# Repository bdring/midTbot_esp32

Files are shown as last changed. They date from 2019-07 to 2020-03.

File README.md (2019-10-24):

# MidTBot ESP32

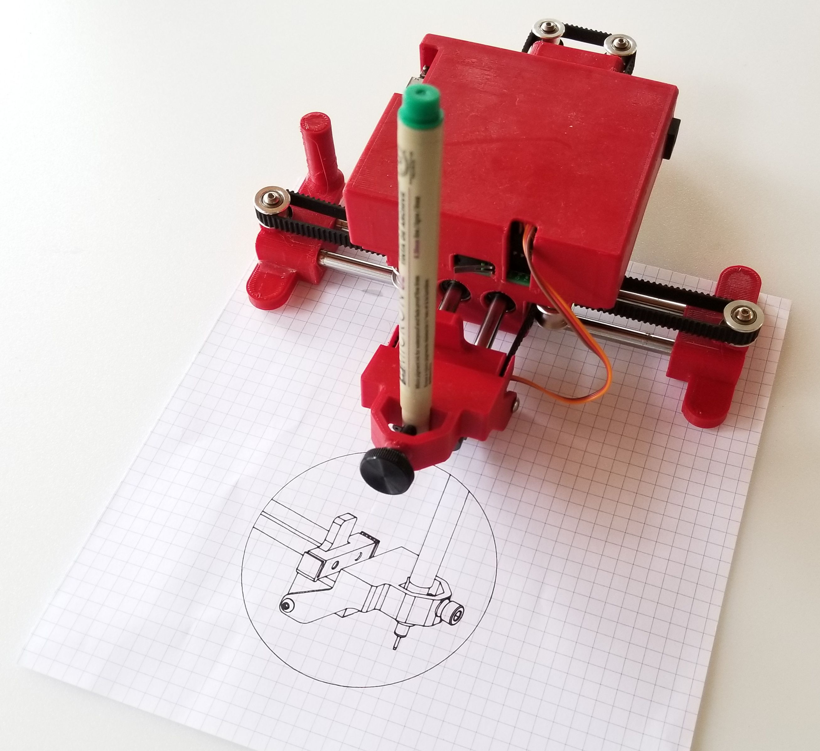
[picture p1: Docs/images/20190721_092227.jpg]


The MidTBot is a small and simple little pen plotter. All of the custom parts are 3D printed. The rest of the parts are low cost and easy to get.

The controller uses an ESP32 running Grbl_ESP32 firmware. It can be controlled via USB, Bluetooth or Wifi. You can simply upload gcode files to the unboard SD card and print.

The machine is controlled by a unique H-bot configuration, that uses a single belt. Two small stepper motors drive that belt in a special way to move in the X/Y plane. The pen is lifted by a hobby servo using a very simple and accurate mechanism.

[Here is a link to a video of the plotter in action.](https://www.youtube.com/watch?v=jiwWCrCfXrY)

The project is open source (Creative commons 4.0 Attribution - Share Alike) and all the files are in this Githob repo. Assembly instructions [are here](https://github.com/bdring/midTbot_esp32/wiki/Assembly-Instructions). If you have questions, please ask them by opening an issue in this repo.

### Check it out on GrabCad

Click on image for interactive viewer in browser.

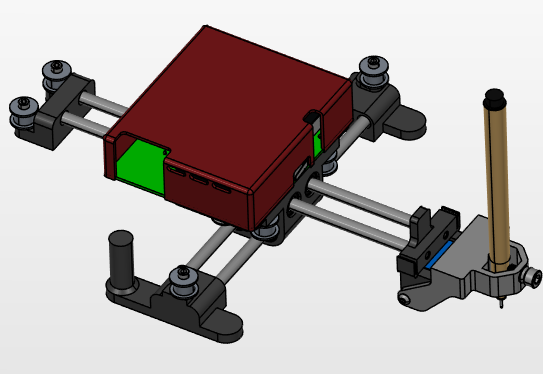
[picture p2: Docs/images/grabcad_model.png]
GrabCAD (https://workbench.grabcad.com/workbench/projects/gcj3zJAQexD3ve_8KkwymatyKXhCWnRs8TB5U1ojGxl3s4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)


### Kits

There currently are no full kits for sale. [Controller kits are available on Tindie](https://www.tindie.com/products/33366583/midtbot-esp32-v1-controller-kit/).

### Donation

This project represents a lot of work. Please consider a safe, secure and highly appreciated donation via the PayPal link below.



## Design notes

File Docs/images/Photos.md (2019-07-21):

### Photos

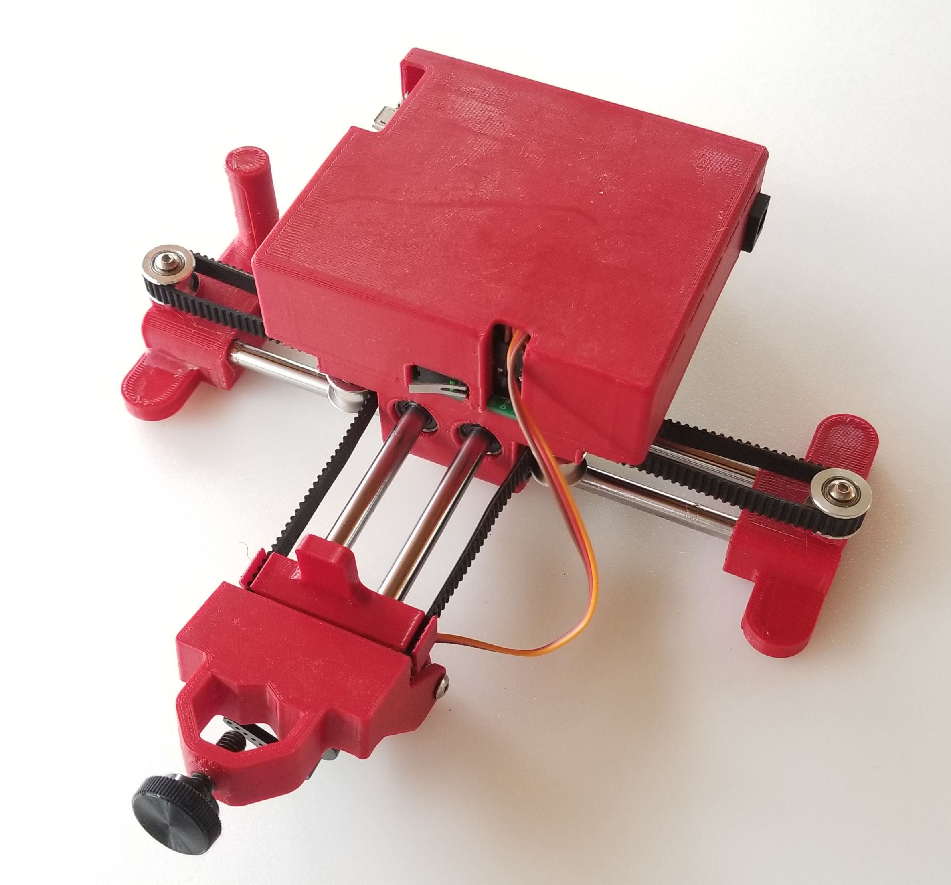
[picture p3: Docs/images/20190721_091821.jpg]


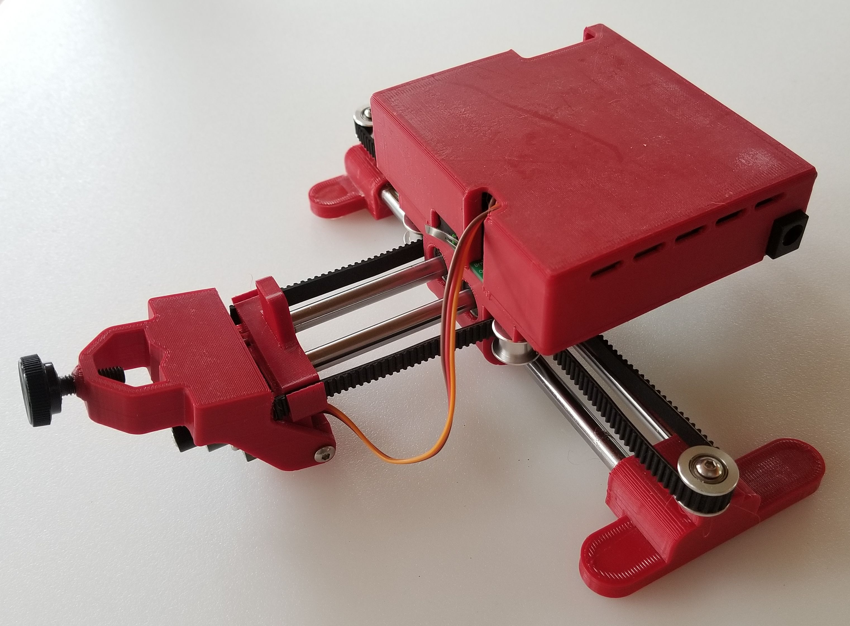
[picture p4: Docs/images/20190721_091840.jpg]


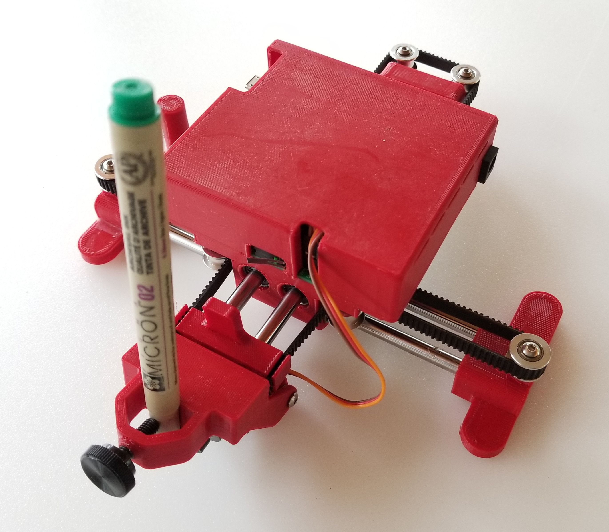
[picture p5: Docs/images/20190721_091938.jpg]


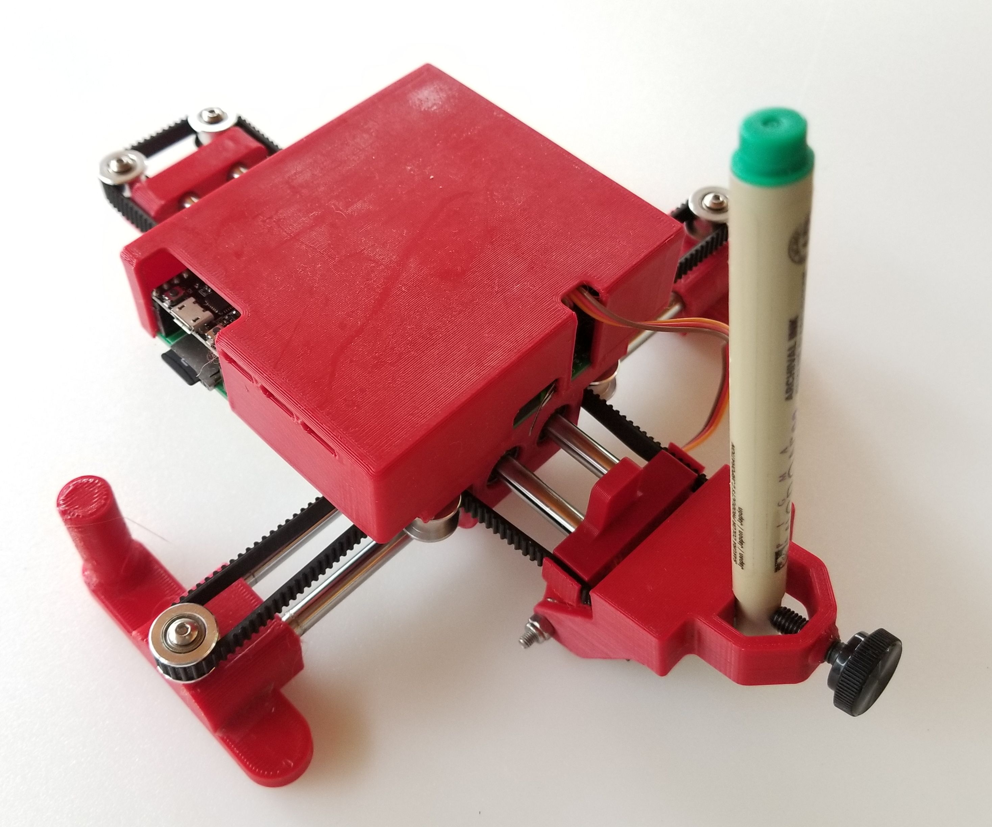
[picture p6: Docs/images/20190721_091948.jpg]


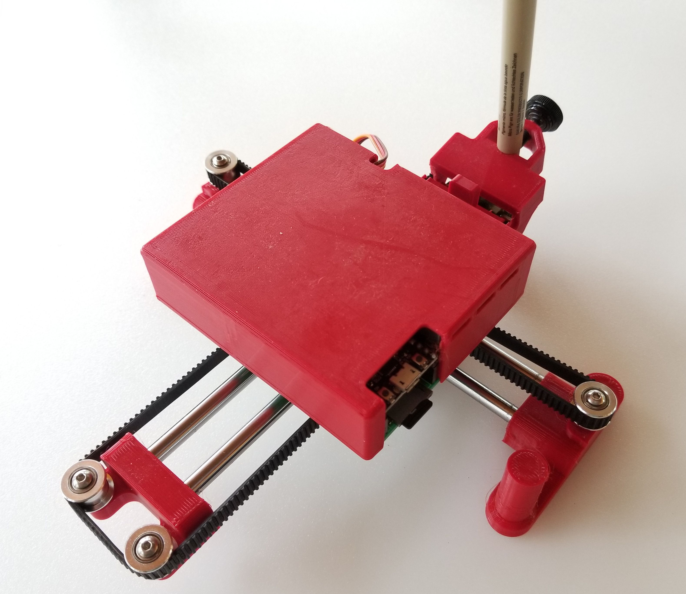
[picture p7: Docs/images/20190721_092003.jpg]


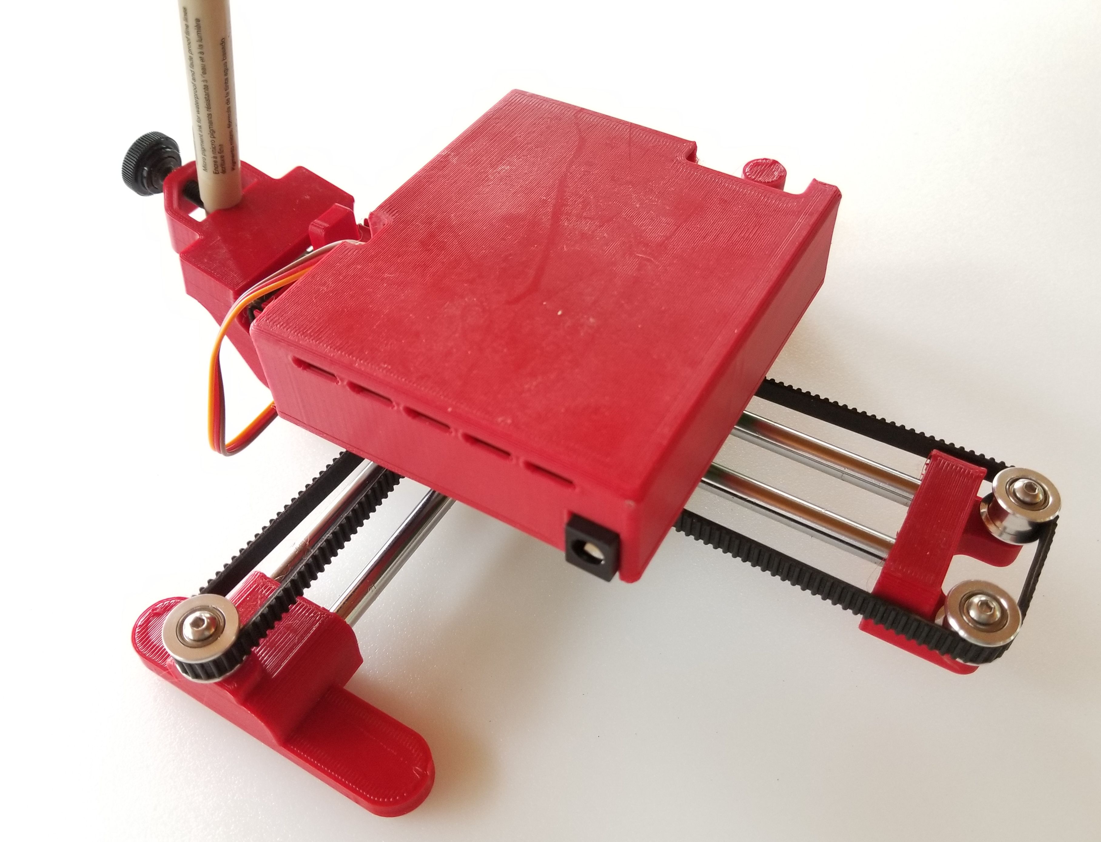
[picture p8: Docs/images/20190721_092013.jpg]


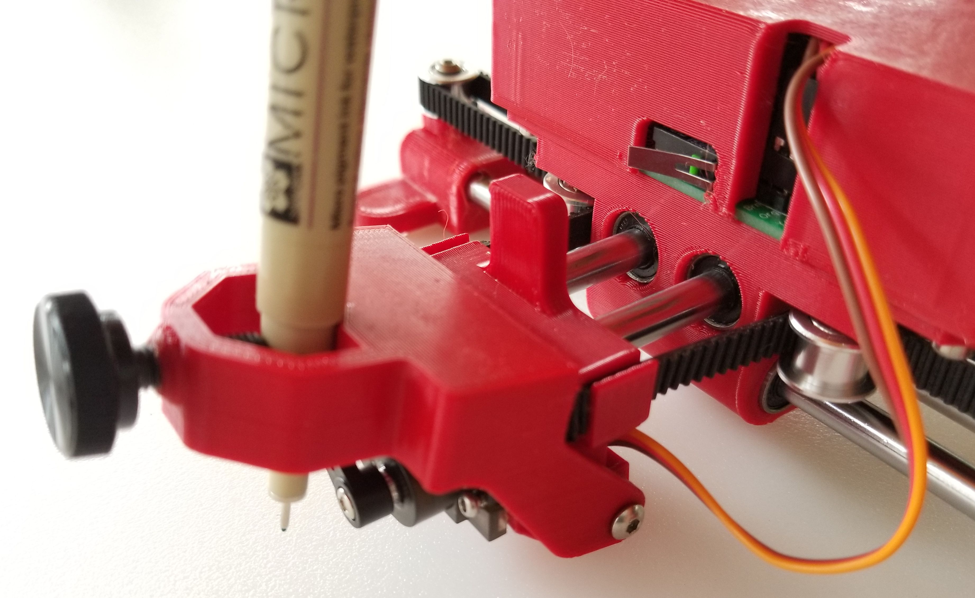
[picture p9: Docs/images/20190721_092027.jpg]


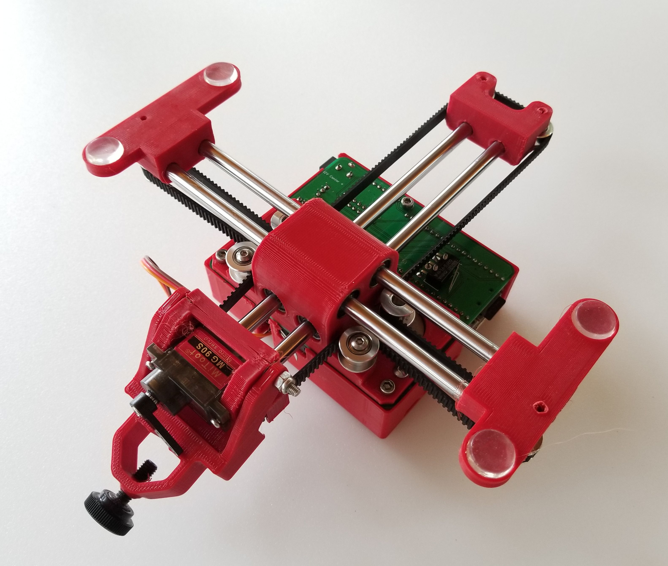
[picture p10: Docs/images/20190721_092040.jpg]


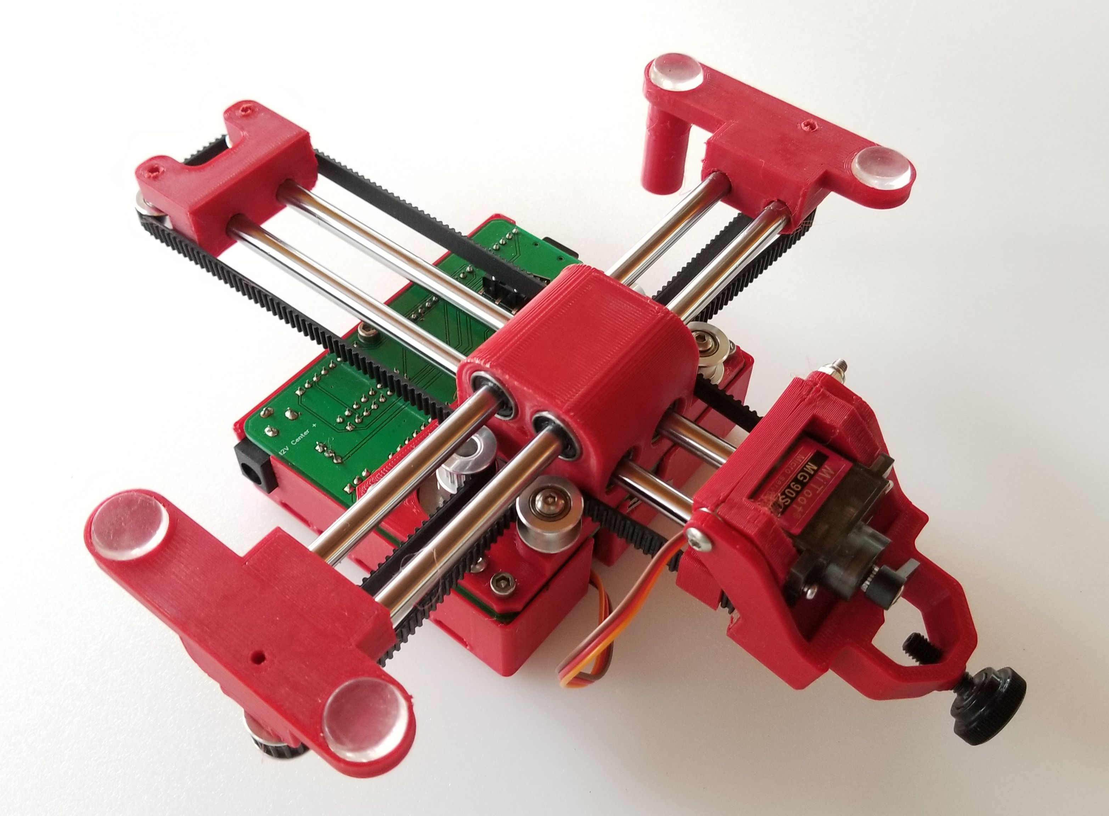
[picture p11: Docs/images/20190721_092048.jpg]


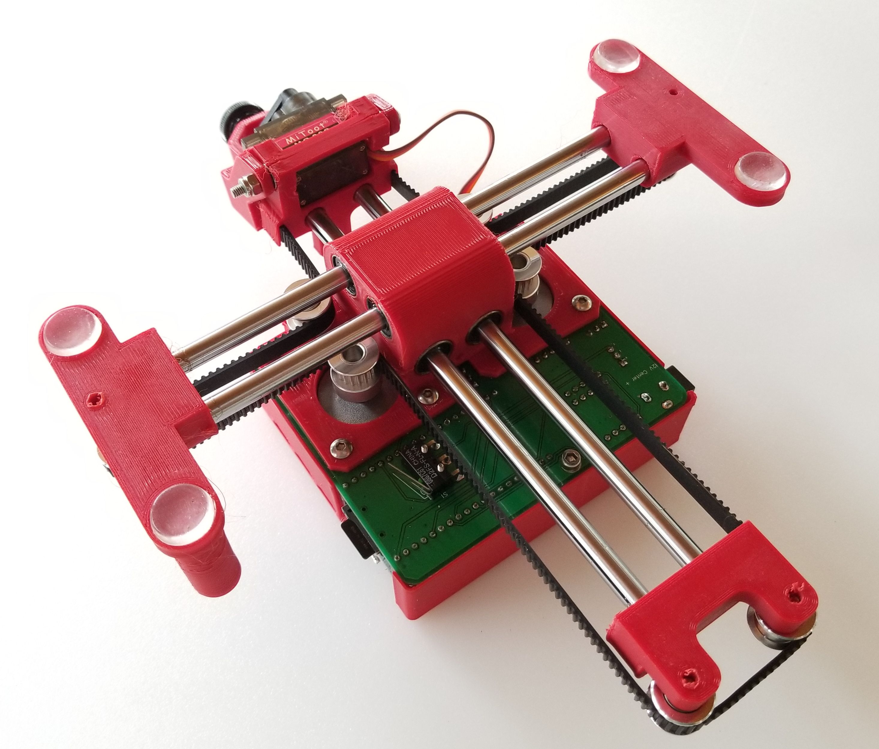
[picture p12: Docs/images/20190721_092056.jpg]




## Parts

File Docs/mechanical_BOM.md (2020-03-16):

### Mechanical Parts List

| Description | Qty  | Source | Help |
| --- | ---- | --- | --- |
| Carriage Block | 1 | 3D Printed | |
| Cover (optional) | 1 | 3D Printed | |
| Left Foot | 1 | 3D Printed | |
| Right Foot | 1 | 3D Printed | |
| Head Block | 1 | 3D Printed | |
| Tail Block | 1 | 3D Printed | |
| Pen Mounting Block | 1 | 3D Printed | |
| Linear Bearing Shaft 6mm Dia. x 200 lg. | 4 | [Amazon](<https://www.amazon.com/ReliaBot-inches-Hardened-Chrome-Plated/dp/B07R16DRVY>) | |
| Linear Bearing LM6LUU (wide Style) | 4 | [Amazon](<https://www.amazon.com/uxcell-LM6LUU-6mmx12mmx35mm-Bushing-Bearing/dp/B01N3MO4FA>) | |
| Pulley GT2 16Tooth 6mm 5mm Shaft | 2 | [Amazon](<https://www.amazon.com/WINGONEER-Aluminum-Timing-Pulley-Printer/dp/B077YHJHVH>) | |
| Smooth Idler Pulley 3mm I.D. 16Tooth Dia 13mm Flange Dia | 6 | [Amazon](<https://www.amazon.com/BALITENSEN-Smooth-Pulley-Toothless-Printer/dp/B077GXV7BJ>) | [Issue](https://github.com/bdring/midTbot_esp32/issues/3) |
| Stepper Motor NEMA14 x 20mm Tall 5mm Shaft | 2 | [StepperOnLine](<https://www.omc-stepperonline.com/nema-14-bipolar-1-8deg-5ncm-7-08oz-in-0-4a-10v-35x35x20mm-4-wires.html>) | [Issue](<https://github.com/bdring/midTbot_esp32/issues/10>) |
| GT2 6mm Wide Belt | 1m | [Amazon](<https://www.amazon.com/Mercurry-Meters-timing-Rostock-GT2-6mm/dp/B071K8HYB4>) | |
| Controller PCB | 1 | | |
| Button Screw M3 x 50mm | 1 | | |
| Hex Nut M3 Locking | 1 | | |
| Socket Head Screw M5 x 14 | 1 | | |
| Socket Head Screw M3 x 16 | 6 | | |
| Button Head Screw M3 x 8mm | 6 | | |
| Rubber Foot 1/2" dia x 1/8" Thk | 4 | [Amazon](<https://www.amazon.com/Self-Stick-Noise-Dampening-Bumpers-12-pieces/dp/B001WAK6DS>) | |
| Bearing 3mm x 7mm x 3mm (683ZZ) | 2 | [Amazon](<https://www.amazon.com/gp/product/B00ZHSR2QU>) | |
| Hobby Servo MG90S | 1 | [Amazon](https://www.amazon.com/s?k=mg90) | |
| 12V 3A Power Supply | 1 | [Amazon](https://www.amazon.com/Adapter-100-240V-Transformers-Switching-Wireless/dp/B073WSWT34) | |

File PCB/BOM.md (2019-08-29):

## MidTBot ESP32 PCB BOM

**Note:** These are the sources I buy from. Many of the parts are available from other sources. Many of the parts are generic and can substituted by other brands. 

| Desg  | Desc | Qty  | Source | Help |
| ----- | --- | ---- | --- | --- |
| C1,C2 | Capacitor, Electrolytic 47uF 35V | 2 | [Digikey](https://www.digikey.com/short/p99tbh) | |
| C3,C4 | Capacitor MLCC 10uF 50V | 2 | [LCSC](https://lcsc.com/product-detail/Multilayer-Ceramic-Capacitors-MLCC-SMD-SMT_SAMSUNG_CL31A106KBHNNNE_10uF-106-10-50V_C13585.html) | |
| J1 | DC Barrel Jack | 1 | [LCSC](https://lcsc.com/product-detail/Power-Connectors_Korean-Hroparts-Elec-DC-005C-20A_C84007.html) | |
| J2,J4 | Header Male 1x4 | 2 | [LCSC](https://lcsc.com/product-detail/Pin-Header-Female-Header_Nextronics-Engineering-Z-211-0411-0021-001_C152150.html) | |
| J3 | Micro SD Socket TF-01A | 1 | [LCSC](https://lcsc.com/product-detail/Connector-Card-Sockets_Korean-Hroparts-Elec-TF-01A_C91145.html) | |
| J5,J6 | Header Male 1x3 | 2 | [LCSC](https://lcsc.com/product-detail/Pin-Header-Female-Header_Boom-Precision-Elec-Header-2-54mm-1-3P_C49257.html) | |
| PS1 | 5VDC 1A Power Supply | 1 | [Digikey](<https://www.digikey.com/short/p993jw>) | [Subs](https://github.com/bdring/midTbot_esp32/issues/12) |
| S1,S2 | Microswitch Switch | 2 | [Digikey](<https://www.digikey.com/short/p993q4>) | [Subs](https://github.com/bdring/midTbot_esp32/issues/2) |
| U1,U2 | Header, Feamle 1x8 | 4 | [LCSC](https://lcsc.com/product-detail/Female-Header_2-54mm-1-8P-Straight-Female-header_C27438.html) | |
| U3 | Header Female 1x19 (FYI: trimming a 1x20 works) | 2 | [AliExpress](https://www.aliexpress.com/item/32760209508.html) | |
| | | | | |
| | **Required Modules** | | | |
| | StepStick A4988 | 2 | | |
| | ESP32 Dev Kit (0.9" Wide Type) | 1 | | |

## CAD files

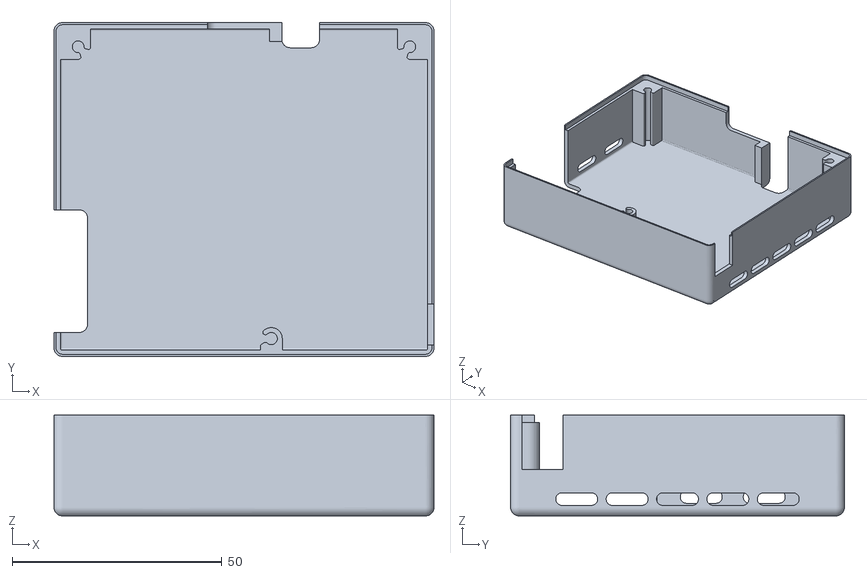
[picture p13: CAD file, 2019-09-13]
STL/midt_esp32_cover_V2.stl
90.5 x 79.5 x 24.0

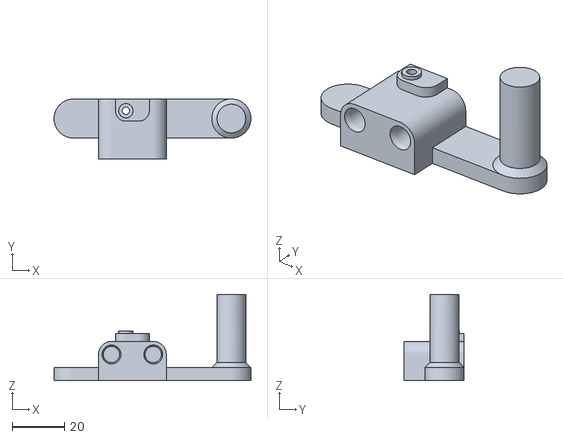
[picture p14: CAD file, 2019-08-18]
STL/midt_esp32_left_foot.stl
75.4 x 23.0 x 33.0

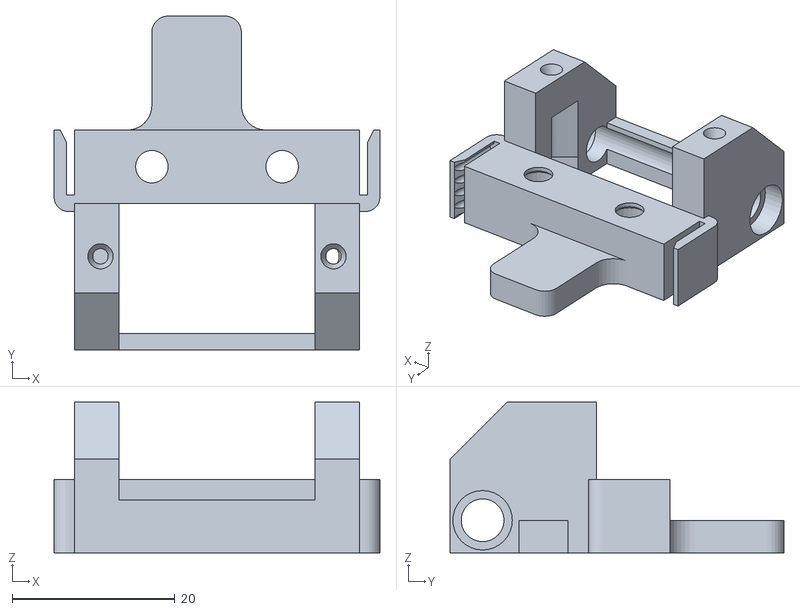
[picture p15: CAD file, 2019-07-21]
STL/midt_esp32_head_block.stl
40.0 x 41.0 x 18.5

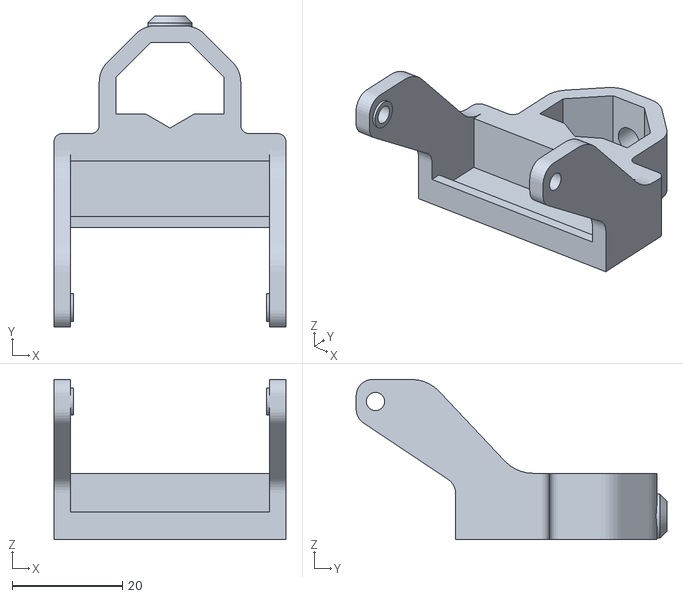
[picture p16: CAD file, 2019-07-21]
STL/midt_esp32_pen_mnt.stl
42.0 x 56.2 x 29.0

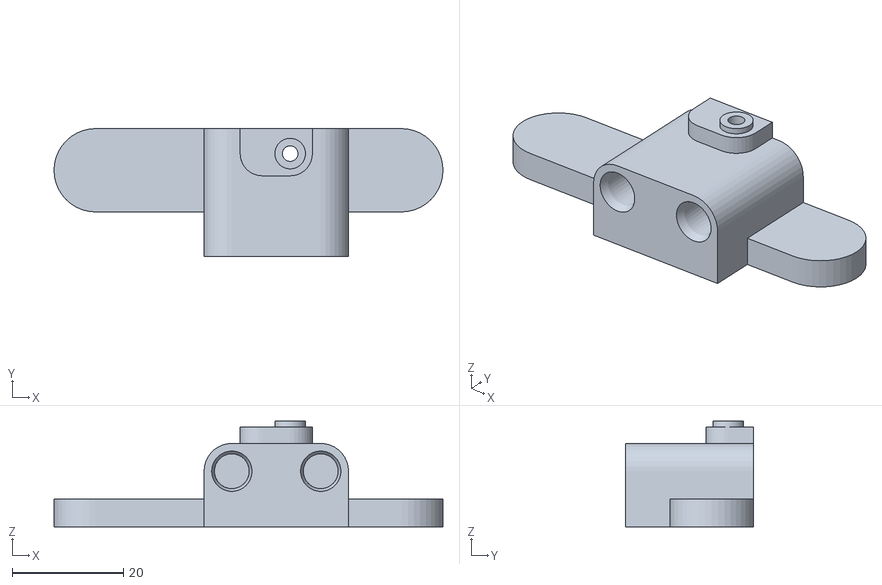
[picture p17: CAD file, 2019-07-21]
STL/midt_esp32_right_foot.stl
70.0 x 23.0 x 19.0

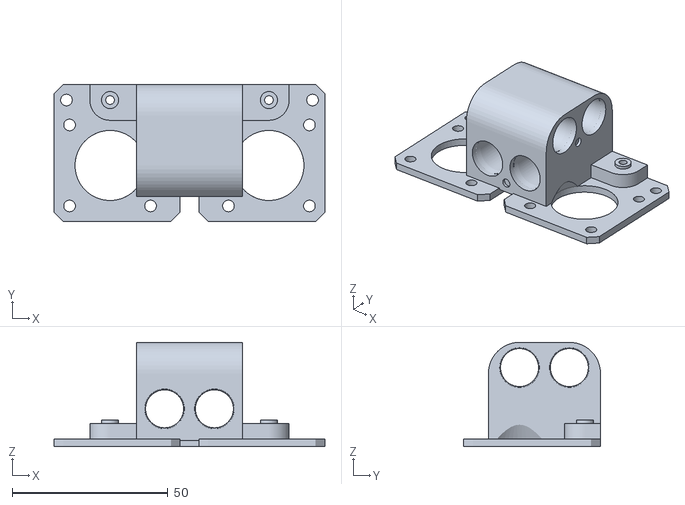
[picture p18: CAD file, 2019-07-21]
STL/midt_esp32_carriage_block.stl
87.0 x 44.0 x 33.5

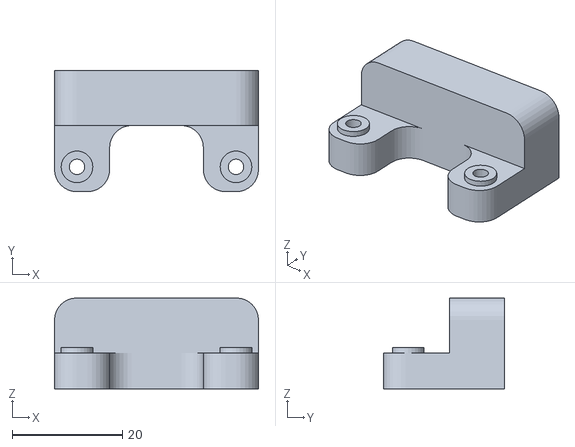
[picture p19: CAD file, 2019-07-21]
STL/midt_tailblock.stl
37.0 x 22.0 x 16.5

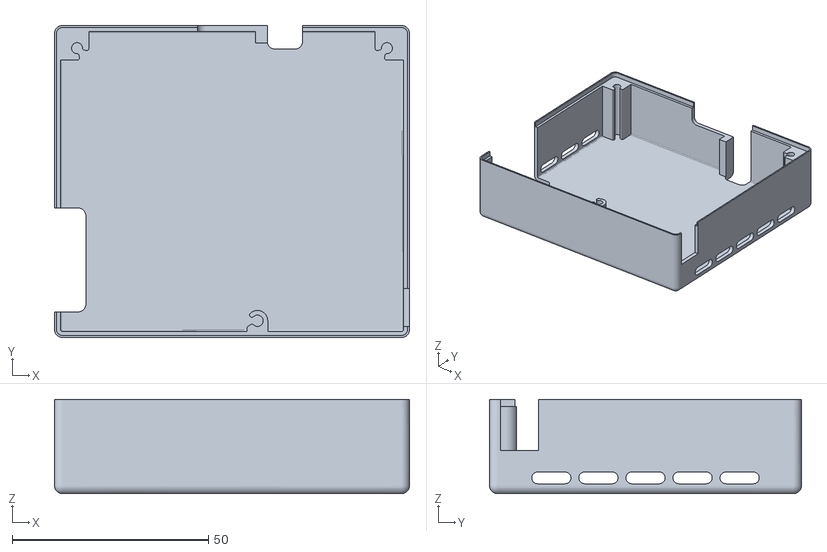
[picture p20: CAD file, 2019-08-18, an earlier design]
STL/midt_esp32_cover_v1.stl
90.5 x 79.5 x 24.0

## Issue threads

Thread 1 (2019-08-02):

Absolutely PHENOMENAL project!

MHeyster, 2019-08-02:
Just wanted to drop a message and say that this is an incredible project, it is extremely well implemented. I'd love to collaborate on the hardware side of you'd be up for it? Send me a message!

bdring, 2019-08-05:
What did you have in mind? We can discuss here or via my [Slack](https://join.slack.com/t/buildlog/shared_invite/enQtNjEzNjMwMTA3ODQ2LTZkMTE5MjcwZTY4MjgwOWEwMWE1MzZlNGNhNDdmMWEwNWZkN2Y5NjBlNjBlZjY2MTg3ZThlN2I3YjEwMzUyMWI)

BTW: I am on vacation in Colorado and will be off grid a lot.

jjgerber01, 2019-08-13:
Hi, 

I went ahead and had the PCB made by PCBGOGO in China. They came out great. Obviously they don't just fabricate 1 board, so I ordered the minimum of 5. I want to build one of these each for me and my daughter and keep a spare. Can I donate the other two boards to you or anyone you know deserving of this? 
Attached are some pictures. I can mail them out. 
Now, just to collect the other parts for it. 
Thanks for the contribution. 

J.J. Gerber 

43 Hollyberry Drive

Paradise, NL, A1L 4A1

Canada

Phone: +1 (709) 749-1612 
E-mail: jjgerber01@yahoo.ca

    On Monday, August 5, 2019, 05:30:06 p.m. NDT, bdring <notifications@github.com> wrote:

What did you have in mind? We can discuss here or via my Slack

BTW: I am on vacation in Colorado and will be off grid a lot.

—
You are receiving this because you are subscribed to this thread.
Reply to this email directly, view it on GitHub, or mute the thread.

jjgerber01, 2019-08-13:
J.J. Gerber 

43 Hollyberry Drive

Paradise, NL, A1L 4A1

Canada

Phone: +1 (709) 749-1612 
E-mail: jjgerber01@yahoo.ca

    On Monday, August 5, 2019, 05:30:06 p.m. NDT, bdring <notifications@github.com> wrote:

What did you have in mind? We can discuss here or via my Slack

BTW: I am on vacation in Colorado and will be off grid a lot.

—
You are receiving this because you are subscribed to this thread.
Reply to this email directly, view it on GitHub, or mute the thread.

PaulHaeberli, 2019-08-13:
Have you found a source for

https://www.digikey.com/short/p993q4

All the suppliers I've tried are out of stock, and it looks like they only

plan to get parts around Dec 26, 2019.

Also, is there a photograph of the board I can use as reference to figure

out where the parts are supposed to go?

Mfg Part Number: D2FS-FL-N-A
Customer PO Number:
Backorder Qty: 10
Ship Method: FEDX GROUND
*Original Delivery Date** *Qty* *Revised Delivery Date** *Qty*
*12/4/2019* 10 *12/26/2019* 10

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

jjgerber01, 2019-08-13:
I had the same problem, but this one matches mechanically. I hope it matches electrically too. You will have to solder some stiff wires inot the PCB and then attach the pins of this switch. The bolt holes aligh well. I inlcuded some pictures with a ruler frm the PCB I had made. 

Gikfun Micro Switch Long Hinge Lever (Pack of 20pcs) forArduino EK1713

by Gikfun_Official_Store

Learn more:https://www.amazon.ca/dp/B06XMQG4TC/ref=cm_sw_em_r_mt_dp_U_pKUuDbDW6YA32

I hope this helps

J.J. Gerber 

43 Hollyberry Drive

Paradise, NL, A1L 4A1

Canada

Phone: +1 (709) 749-1612 
E-mail: jjgerber01@yahoo.ca

    On Tuesday, August 13, 2019, 01:54:24 p.m. NDT, PaulHaeberli <notifications@github.com> wrote:

 Have you found a source for

https://www.digikey.com/short/p993q4

All the suppliers I've tried are out of stock, and it looks like they only

plan to get parts around Dec 26, 2019.

Also, is there a photograph of the board I can use as reference to figure

out where the parts are supposed to go?

Mfg Part Number: D2FS-FL-N-A
Customer PO Number:
Backorder Qty: 10
Ship Method: FEDX GROUND
*Original Delivery Date** *Qty* *Revised Delivery Date** *Qty*
*12/4/2019* 10 *12/26/2019* 10

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

—
You are receiving this because you commented.

Reply to this email directly, view it on GitHub, or mute the thread.

bdring, 2019-08-13:
I started a [new issue](https://github.com/bdring/midTbot_esp32/issues/2) to discuss sourcing the switch.

@jjgerber01

renschler, 2019-08-13:
@jjgerber01 if you still have PCBs to spare i'd be interested in buying one or two off you

@bdring great project! thanks for sharing

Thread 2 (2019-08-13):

Limit Switch Sourcing

bdring, 2019-08-13:
The [switch on the BOM](https://www.digikey.com/short/p993q4) is hard to get.  Here are some possible alternatives.

[This version](https://www.digikey.com/product-detail/en/omron-electronics-inc-emc-div/D2FS-FL-N-A1/SW1985-ND/4753391) has a reversed lever. It will definitely work on the Y axis. It will probably work on the X, but the actuator post is not in the ideal location on the lever.

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

[This amazon switch](https://www.amazon.ca/dp/B06XMQG4TC/ref=cm_sw_em_r_mt_dp_U_pKUuDbDW6YA32) won't work. You need right angle terminals.

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

This type of [switch from AliExpress](https://www.aliexpress.com/item/859187710.html) is fits. It just has the lever reversed like mentioned above.

Search for [DF2-L-A](https://www.aliexpress.com/wholesale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) on AliExpress for more options

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

dirkx, 2019-08-17:
[Farnell #2402447, €0.88](https://nl.farnell.com/omron-electronic-components/d2fs-fl-n-a/microswitch-lever-spst-0-1a-6vdc/dp/2402447)
[mouser[(https://nl.mouser.com/ProductDetail/Omron-Electronics/D2FS-FL-N-A) and
https://nl.aliexpress.com/item/33032594245.html
https://nl.aliexpress.com/item/32802131724.html
https://nl.aliexpress.com/item/32881389932.html

bdring, 2019-08-18:
The design has been [updated](https://github.com/bdring/midTbot_esp32/commit/2eb69e2da447061a77404fdc40bd8de124e4595f) to allow both lever positions to work.

- The X actuator post was moved back 5.4mm
- The cover was modified to clear the lever.

bdring, 2019-08-28:
I was wrong about the alternate lever position. The lever is not reversed, the leads are just bent the other way. This means it will switch around some pins if you solder it that way. It is basically upside down. This won't work right.

The simple fix is to just bend the leads back to the original position. I have done this on dozens of switches now and it is safe and effective.

Closed 2019-08-18.

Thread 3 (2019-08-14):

Idler sizing

dirkx, 2019-08-14:
The BOM should probably stress that the idlers need to be fairly small; with an OD of the rims of 13 or even less. (as standard idlers for 2GT tend to be around 22-24mm).
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

bdring, 2019-08-14:
I typically use toothless idlers. Several of the idlers touch the back of the belt.

They are usually matched to the equivalent tooth size. The ones I use are 16 tooth equivalent diameter.

I'll try to find  a way to link to link the BOM item to a page with more detailed dimensions.

bdring, 2019-08-14:
Here are the dimensions for the smooth idler.

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

dirkx, 2019-08-15:
On 15 Aug 2019, at 00:18, bdring <notifications@github.com> wrote:
> I typically use toothless idlers.
>

Drawing was a bit confusing. The main point is that most default idlers and pulls with tooth have a larger rim OD than the ones that currently easily fit. And this is rarely part of the spec-sheet.

So it would be good to update the BOM to stress the much smaller than `default' size of the outer rims. And ultimately adjust the design a bit perhaps to allow the more common 22-25mm outer diameter idles (the inner diameter is only 2-3mm larger than yours).

Dw

bdring, 2019-08-15:
I added more info to [BOM](https://github.com/bdring/midTbot_esp32/blob/master/Docs/mechanical_BOM.md) and a link to this issue.  Changing the pulleys would affect many parts, increase the size and reduce the work area. I don't want to do that.

Closed 2019-08-18.

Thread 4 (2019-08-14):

Width of the ESP32 Dev kit (0.96)

dirkx, 2019-08-14:
It appears that a fair number of ESP32 dev kits (13/26 pin version) sold as 0.96 wide are wider than what fits on the circuit board. Simply adding a row of 13 holes next to the current one; with the usual spacing, would accommodate both.

bdring, 2019-08-14:
That is a feature I have added to many of my other ESP32 projects. Typically it is a 19 pin connectors with 0.9" and 1.0" pitch.

Do you have details on the 0.96" part?

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

dirkx, 2019-08-15:
Yes - that layout should work splendidly - and there is just enough room for it.
I'll try to make a list of the amazon/aliexpress URLs with the 'sizes' .

dirkx, 2019-08-17:
So actual width on aliexpress, amazon & ebay for the units (17# units, 5 vendors) sold as 13 pin / 0.96"(24.4mm)  seems to be closer to 26mm if they are not exactly  0.96" as specced (3#). And 5 units are exactly 0.1" wider.

So the extra row straight against the current 0.96 would cover all these nicely.

bdring, 2019-08-17:
You you have a link and picture for the 13 pin 0.96" modules?

dirkx, 2019-08-29:
Photo's and solution below.

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

bdring, 2019-08-29:
I am still unclear on the 13 pins?

JamesCWhite, 2019-08-30:
Pretty sure the .96" measurement from most listings refers to the oled size, even if it's a model without one. The way those sellers copy each other's listings, it's probably reused from a listing for one with a screen.

dirkx, 2019-08-30:
If - that -  I just got a batch from one DE reseller with 2 ‘narrow ones’ and 8 wider ones (so 0.96 and the other 2.54mm wider). And had the same a while ago on Aliexpress.

Guess the standard is ‘both’. :)

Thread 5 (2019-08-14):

Improvement request: labeling of stepper motors

dirkx, 2019-08-14:
Would be nice to mark pin 1 of the stepper connectors and the 1A,1B, 2A, 2B on the top of the board.

bdring, 2019-08-14:
I don't follow completely. Could you markup a screen shot?

dirkx, 2019-08-15:
12/AB labels - as these are often on the datasheets with wire-colours of the steppers.

And a pin 1 marker - as a lot of connectors have such a marker too.

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

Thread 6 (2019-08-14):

Feature/improvement: through the hole capacitors

dirkx, 2019-08-14:
Would be nice to also have hole-pads for the 4 SMD capacitors. So you have the option.

Probably not practical for the SD slot - as those are (too) hard to get in through the hole versions.

bdring, 2019-08-14:
These days most people are getting pretty comfortable hand soldering things like 1206 and 0805 caps. I don't want to change those parts.

The SD card is a PITA, but there are not too many options. On my first test controller, I used a standard SD card module. I don't know if there is a way to fit that and still make the card accessible.

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

bdring, 2019-08-18:
Checked: There is no good location for the standard micro SD card module.

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

closing issue

Closed 2019-08-18.

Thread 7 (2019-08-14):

Improvement request: labeling of DC/DC pins

dirkx, 2019-08-14:
Would be nice to have the Vin, GND and Vout labels on the silk screen for the 5V DC/DC.

bdring, 2019-08-14:
Good suggestion. That will be included on future versions.

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

dirkx, 2019-08-15:
Lovely - thanks !

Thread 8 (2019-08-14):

Improvement request: screw terminal

dirkx, 2019-08-14:
Would be nice to have two screw terminal holes in addition to the normal barrel style socket. With +12v/GND labeling. For balance reasons - having it in the middle back of the board at the bottom may be nice.

bdring, 2019-08-14:
I don't want to increase the board size at all. The back concerns me. It could tend to rub on the Y axis and there is not much space, especially if a second row of CPU pins is added.

Here is a possible overlapping footprint, that allows you to chose barrel or terminal block.

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

dirkx, 2019-08-15:
Splendid - that would work. Would be nice to also label the silk screen.

dirkx, 2019-08-17:
Just rechecked, tried and find that a screw terminal just next to the bolt hole for the casing  and right of the 'V1" label at the back of the board works well - and 'balance' wise is nicer than the current barrel  connector location.

bdring, 2019-08-18:
I don't think it will fit after the dual footprint is added.

Also keep in mind the cover needs over a 1mm clearance around the perimeter.

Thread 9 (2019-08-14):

patch - some minor instruction updates

dirkx, 2019-08-14:
Hm - seem unable to do a PR on the wiki - possible suggestion below.

Dw.

https://github.com/dirkx/midTbot_esp32.wiki.git
https://github.com/dirkx/midTbot_esp32/wiki

commit 0b3bfede5c0680eb9977cf97de8946958ef01d95 (HEAD -> master)
Author: Dirk-Willem van Gulik <dirkx@webweaving.org>
Date:   Wed Aug 14 13:25:35 2019 +0200

    Grbl over normal OTA limit, different model needed.

commit 31539e975a2bfafa1c698348e62e8c25fbccbb00 (fork/master)
Author: Dirk-Willem van Gulik <dirkx@webweaving.org>
Date:   Wed Aug 14 13:07:33 2019 +0200

    Set travel to ensure homing works, current

diff --git a/Compiling-Firmware-for-the-MidTBot.md b/Compiling-Firmware-for-the-MidTBot.md
index 1a77aac..2a12545 100644
--- a/Compiling-Firmware-for-the-MidTBot.md
+++ b/Compiling-Firmware-for-the-MidTBot.md
@@ -8,4 +8,10 @@ to...

 #define CPU_MAP_MIDTBOT // these are defined in cpu_map.h

-Follow the [compile instructions](https://github.com/bdring/Grbl_Esp32/wiki/Compiling-the-firmware).
\ No newline at end of file
+Follow the [compile instructions](https://github.com/bdring/Grbl_Esp32/wiki/Compiling-the-firmware).
+
+#### Memory
+
+As the standard ESP32 DevKits come with 4 Mbyte of memory - you will typically be required to select the large-app/minimal OTA memory layout. As otherwise you will get an error that the sketch is too large.
+
+
diff --git a/Setting-Up-the-Motors.md b/Setting-Up-the-Motors.md
index 8ace504..6f2a63f 100644
--- a/Setting-Up-the-Motors.md
+++ b/Setting-Up-the-Motors.md
@@ -4,6 +4,13 @@

 The MidTbot uses the CoreXY feature of Grbl_ESP32. With a CoreXY machine both motors must coordinate motion even for simple moves along one axis. If an axis moves the wrong way, you cannot simply change the $3 setting for that  axis. You must leave the $3 settings for X and Y at the default of 0 and correct the direction issue with the wiring.

+#### Setting Motor Current.
+
+The motor drivers have a potentiometer to adjust motor current. You want the motor to run just a little warm. If they get too hot, adjust the pot to lower the current. Search for documentation on your driver for more specific details.
+
+In general - the prescribed StepStick A4988 should have their pot-meters adjusted to the lowest current -- by turning them all the way anti-clockwise. And then about 1/5 to 1/4 of the scale back up. Increase this slightly if you find that the motor stalls during the below process. Or go anti-clockwise if they get too hot.
+
+
 #### Reseting Default settings

 Set $rst=$ to reset all of the default Grbl settings. This will make sure any previous settings that could be in the controller.
@@ -20,11 +27,9 @@ Rotate a connector and retry the direction moves. There are 4 possible orientati

 #### Homing Test

-Send $H to home the machine. It should home the X axis first, then the Y. Each axis should move towards the limit switch mounted on the PCB.
+Send $H to home the machine. It should home the X axis first, then the Y. Each axis should move towards the limit switch mounted on the PCB.

-#### Setting Motor Current.
-
-The motor drivers have a potentiometer to adjust motor current. You want the motor to run just a little warm. If they get too hot, adjust the pot to lower the current. Search for documentation on your driver for more specific details.
+Note that the default X/Y travel range of Grbl is 100mm; you want to increase this to 150mm first.

 ------

@@ -36,7 +41,7 @@ The horn needs to be mounted on the servo at a precise angle. This  will be done

 #### Test the Motion

-Plug the servo connector into the PCB and power on the controller. Clear the homing alarm by sending $X over the serial port. Next send $rst=#. This will reset any machine offsets that might be in memory. Send G0Z5 the servo should move to one end of the travel. You can see the other end of the travel by sending G0Z0. Send G0Z5 again to move to the pen up position. The servo should be rotating clockwise to lift the pen and counterclockwise to lower it.  Not all servos travel the same way. If yours is going the wrong way, send $3=4 to reverse the Z direction.
+Plug the servo connector into the PCB and power on the controller. Clear the homing alarm by sending $X over the serial port. Next send $rst=#. This will reset any machine offsets that might be in memory. Send G0Z5 the servo should move to one end of the travel. You can see the other end of the travel by sending G0Z0. Send G0Z5 again to move to the pen up position. The servo should be rotating clockwise to lift the pen and counterclockwise to lower it.  Not all servos travel the same way. If yours is going the wrong way, change the $3 by adding '4' (So $3=6 assuming $3=2 as per the defaults) to reverse the Z direction.

 #### Install The Horn

@@ -48,9 +53,4 @@ Now test the servo, by sending G0Z0 and G0Z5 a few times. The pen mechanism shou

 Typically Z5 will be close to where you want because that is how you installed the horn. Z0 might be moving past the point at which the pen is fully down, so you might need to send a $102 value above 100. The valid ranges are 20 to 180. If you go outside that range, it will ignore the value and use 100.

-
-
-
-
-

bdring, 2019-08-14:
I'll incorporate some of these suggestions when I get home from vacation 8/19.

Regarding anything with changes to $ settings. It is better to change the defaults in firmware.

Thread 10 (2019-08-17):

Update BOM / ease procuring of stepper motors

dirkx, 2019-08-17:
The currently specced/linked stepper motor [link](https://www.omc-stepperonline.com/nema-14-stepper-motor/nema-14-bipolar-18deg-5ncm-708ozin-04a-10v-35x35x20mm-4-wires-14hs08-0404s.html) in the [bom](https://github.com/bdring/midTbot_esp32/blob/master/Docs/mechanical_BOM.md) has a fairly short axis (12.5mm length).

Actual round axis length can be up to 22mm to still clear the left/right feet.

So would suggest updating the BOM to allow up to 20.8mm of shaft length.

And perhaps clarify that the mentioned 20mm body/enclosure size is not that critical.

As that means there are many more stepper motor suppliers suddenly.

bdring, 2019-08-18:
The stepper motor must be a NEMA14 with 5mm shaft.

The height of the body of the motor must be 20mm or less to fit the standard cover. A taller motor is fine if you don't use a cover or design a deeper one.

The motor shaft on the one listed in the BOM is rather short. I can be up to about 20mm long.

I have linked this issue to the BOM.

Closing issue.

bdring, 2019-10-15:
[Here is an amazon link for a motor that should work.](https://www.amazon.com/gp/product/B00PNEPQ8E/ref=ppx_od_dt_b_slice_asin_title?ie=UTF8&psc=1)

Closed 2019-08-18.

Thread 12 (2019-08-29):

Alternative to the 5V DC-DC Power Supply

bdring, 2019-08-29:
I have tested [this power supply from Alibaba](https://www.aliexpress.com/item/33034496914.html?spm=a2g0s.12269583.0.0.255713f1OnfaJm) and it works fine. It has a variable output rather than a fixed one, so it does need to be adjusted.

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

niekproductions, 2019-08-29:
I'm using [this fixed voltage one](https://nl.aliexpress.com/item/32950632281.html). It's a bit taller than a standard 7805, so you need to bend it forward a bit for the top cover to fit on. Otherwise it works fine!

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

dirkx, 2019-09-07:
These ones https://nl.aliexpress.com/item/32787145932.html work splendidly as well. They back of the board need to be facing 'outward'; the side with the pins inward.

admin-kepo, 2020-03-21:
can i replace it with IC L7805?

dirkx, 2020-03-21:
You can - but it will get very hot and will need a very sizable cooling fin.

aixlds, 2020-03-30:
Thank you for responding quickly to my question, If so I will try it with other modules that are similar because there are very few modules available in my place.

admin-kepo, 2020-03-30:
Thank you for replying, in the end I tried using a module that I found from aliexpress

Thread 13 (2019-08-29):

Pen is lowered onto the paper after homing

niekproductions, 2019-08-29:
After completing the homing cycle, the bot proudly drops the pen down on the paper which leaves an unwanted dot in that spot.
Is there a way to disable this, and keep the pen up?

bdring, 2019-08-30:
I think there is a way to avoid that, but it will require some changes to the firmware. I'll look into that over the weekend.

bdring, 2019-08-31:
Fixed

I updated the firmware. The devt branch has the changes. Firmware changes are tested there before moving to the master branch.

The midTbot only homes the X and Y axis, but the servo axis feature of Grbl_ESP32 allows you to tell the servo what to do while the other axes are homing. It is setup to go to the max travel (z=5mm) while the other axes are homing. After homing is complete is goes to the current Z value. That value is set to a machine coordinate system value of 0 on all non homed axes. Z is a non homed axis. Therfore the Z was going to the down position after homing

You can have the servo use the machine coordinates or the work coordinates. Work coordinate systems allow you to do do things like set 0,0,0 points anywhere in the travel. Previously it was set to machine coordinates. I changed to use a work coordinate system. This allows you to offset the work coordinate system from the machine coordinate system by 5mm. This means when the machine system gets set to Z0 the work coordinate system is Z5, so the pen stays up.

You need to set the offset manually. You only need to do this once, because the machine will store it in flash memory. Send **G10L2P0Z-5** via a serial console or the console in in the WebUI.

You will need to compile and upload new firmware. Follow the [instructions](https://github.com/bdring/midTbot_esp32/wiki/Compiling-Firmware-for-the-MidTBot) here, but use the [Devt branch](https://github.com/bdring/Grbl_Esp32/tree/Devt).

I will update this post when it moves to the master branch

momo-aux, 2020-01-09:
Mine still drops the pen. Flashed this week with master. Is there a workaround or do I have to compile the dev Version

bdring, 2020-01-09:
I'll double check the master branch when I get home tomorrow.

bdring, 2020-01-10:
Just tested with latest master. It seems to be working fine for me. The CPU_MAP has a few features that control the behavior during homing.

```
#define SERVO_Z_HOMING_TYPE		SERVO_HOMING_TARGET // during homing it will instantly move to a target value
#define SERVO_Z_HOME_POS		SERVO_Z_RANGE_MAX
```

The servo should immediately go up when homing.

Are you sure your servo is going the right way? Try sending G0Z5 and G0Z0. Does it move up for Z5 and down for Z0? If not, send $3=4 to reverse the Z.

momo-aux, 2020-01-10:
Yes, its going up on G0Z5 and down on G0Z50
It is moving up before homing X but after Homing X it goes down.

This only happens when homing for the first time.
After I raised the pen one time it stays up after homing.
But before homing the first time, I cant raise it. So it happens always after reconnecting the power and do homing for the first time.

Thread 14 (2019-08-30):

No ESP32 chip listed in the BOM

dwightmulcahy, 2019-08-30:
Docs/mechanical_BOM.md does not list the ESP32 chip to get.

here is a link to ESP32 Dev:
https://www.amazon.com/HiLetgo-ESP-WROOM-32-Development-Microcontroller-Integrated/dp/B0718T232Z

~~Or this one for two:
https://www.amazon.com/MELIFE-Development-Dual-Mode-Microcontroller-Integrated/dp/B07Q576VWZ~~

bdring, 2019-08-31:
Do not get the second one. It has the wrong number of pins.

It needs to be 19x2 with a pin width space of 0.9". Do not get the 15x2 version or the 19x2 1.0" width version.

dwightmulcahy, 2019-08-31:
Ugh, thanks...

the specs on these seem hard to find but this one seems to meet the needs, 19x2 and ~0.89" pin spacing:
https://www.amazon.com/KeeYees-Development-Bluetooth-Microcontroller-ESP-WROOM-32/dp/B07QCP2451

bdring, 2019-08-31:
Most of my boards support the (2) widths of the 19x2 types.  I'll be adding this to the next rev of the PCB. I'll be ordering and testing it before I post it.

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

dwightmulcahy, 2019-09-03:
nice.  I bought one of the v1 boards that you had...

dwightmulcahy, 2019-09-04:
ended up getting this one: https://www.amazon.com/gp/product/B0718T232Z

closing this issue as the PCB/BOM.md lists the need for an ESP32 Dev Kit (0.9" Wide Type).

Closed 2019-09-04.

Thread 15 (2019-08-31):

Unstable Y axis

niekproductions, 2019-08-31:
My midTbot is working great, but I've noticed that there is an increase in vertical play as the head gets further away from the X axis. It's up to around 5mm when fully extended, making the head drag across the paper. This also makes it more difficult to find a good pen height where it touches the paper across the full drawing surface.

Is this a common issue, or could I have bad bearings/rails?

bdring, 2019-08-31:
There should be no play in the Y axis. If there is a little play, it will exaggerate as the axis moves out. Try to find where the play is and fix it.

Not all printers have the same performance when creating hole sizes. If you have a rod or bearing that is loose in a hole, you may need to tweak to hole diameter. Many CAD programs, like fusion 360,  allow you to tweak STEP files. You also may be able to change some settings in your slicer.

niekproductions, 2019-08-31:
Thanks, I'll investigate where the play is. I suspect cheap bearings, but might have to tweak my parts as well.

I've already adjusted the hole diameter to have zero clearance, as the original parts had a very loose fit. Would you like me to post the new STLs somewhere?

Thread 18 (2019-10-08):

plot file(s) with push button(s) ?

snug11, 2019-10-08:
hi all,
i`m asking for a possible (firmware) extension:
there are a few unused gpio`s on the esp32...could them be used to start different plot files by pushing buttons (internal pullup on/gnd) with ?

for example:
gpio32/button1 = plot file "xxx.gcode"
gpio33/button2 = plot file "yyy.gcode"
(for best, pin assignment in ui under "sd-files area", beneath each loaded file)

that would be absolute easy to let guests (on a faire) start plotting different preloaded grahics without the needing of a second device (laptop, smartphone...)

...that would be great !  :-)

with kind regards from germany
andree

JamesCWhite, 2019-10-12:
See here:
https://github.com/bdring/Grbl_Esp32/wiki/Macro-Button-Feature

snug11, 2019-10-15:
I'll try it, thanks for showing that!  :-)

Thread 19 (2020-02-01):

How to setup bluetooth?

BigDave365, 2020-02-01:
What is the best way to control the plotter via bluetooth (Windows 10)?

I assume a virtual com port, but don't know where to start on the windows side or the plotter side.

Thanks....

bdring, 2020-02-01:
The controller needs to have Bluetooth enabled.

Make sure **#define ENABLE_BLUETOOTH** is not commented out in **config.h**
Give the Bluetooth a name with **[ESP140]MyBtName**
Put the radio in Bluetooth mode with **[ESP110]BT**

Connect from Windows.
Do an **Add a Bluetooth Device** from Windows.
It will create 2 new COM ports. Typically one is used by Windows to deal with the connection. The other can be used by you just like a regular COM port. Typically the higher number port is the one you use.

BigDave365, 2020-02-01:
Yeah that would have taken a while to sort out....

I do not understand the commands below:

Give the Bluetooth a name with [ESP140]MyBtName
Put the radio in Bluetooth mode with [ESP110]BT

Do I enter this on the command line on the terminal?

This is my first foray into CAM (other than 3D printers), so sorry for all the questions.

Thanks for the help, I'll give it a go this afternoon.

bdring, 2020-02-01:
This GitHub repo is specific to the midtbot machine. These questions are more targeted at [Grbl_ESP32 firmware](https://github.com/bdring/Grbl_Esp32). You might find better resource on that repo.

The commands can be entered on any communications interface (USB,BT,Wifi), but USB is easiest because it is always on. It also gives a bunch of information when Grbl_ESP32 starts. This is before you could establish a wireless connection. It will tell you the Bluetooth or Wifi modes, addresses, etc.

The default USB/Serial settings are 115200,N,8,1. I would use the Arduino IDE serial monitor setup like below. (use your com port number of course)

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

You can click the reset button on your ESP32 to see all the boot information. All Grbl_ESP32 specific information is in this format [MSG: ....]

Closed 2020-03-17.

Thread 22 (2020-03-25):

sdcard

vascobarbosa, 2020-03-25:
install it with this esp32 dev board

https://cdn.shopify.com/s/files/1/1509/1638/files/ESP_-_32_NodeMCU_Developmentboard_Pinout_Diagram.jpg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

but the sd card is not working, everything works, web ,through bluetooth, via telnet, via usb cable
but the sd_card is always not found.

though about remapping the pins, but I guess I wanted to ask first if somebody had a clue

bdring, 2020-03-25:
Check the soldering of the SD card socket. We have seen a few poor connections on one of the batches. If you gently push each pin down with a soldering iron, that fixes it.

vascobarbosa, 2020-03-25:
thanks, gonna check them,

vascobarbosa, 2020-03-25:
Checked and rechecked the connections

with the multimeter everything is connected right, and on the right pins

on the we_gui I get always no SD card, and on the computer it works and format in fat32
on a mac osx

This is weird, and sorry about this, but this isnt one of your batchs, had some credits at jlcpcb.com and made them done some boards

bdring, 2020-03-25:
I would still suspect the soldering. Those pins can bend up during handling and not solder correctly.

Also see the [wiki about formatting the SD card](https://github.com/bdring/Grbl_Esp32/wiki/Using-the-SD-Card).

vascobarbosa, 2020-03-25:
fixed it, BAD SD FORMATING

On OSX open the terminal and follow this commands

#mount
/dev/disk2 on / (hfs, local, journaled)
devfs on /dev (devfs, local, nobrowse)
/dev/disk3s1 on /Volumes/USB_Disk (msdos, local, nodev, nosuid, noowners)
**In this case, my disk is disk3. Your disk will most likely be different! Be sure to reference the correct disk - you can and will lose your data if you format the wrong drive!!!**

3) Unmount the disk
#diskutil unmountDisk disk3
Unmount of all volumes on disk3 was successful

4) Format the drive
#sudo newfs_msdos -F 16 /dev/disk3
After a few moments, your drive will format.And it will work

Closed 2020-03-26.

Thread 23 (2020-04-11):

Missing stepper motor drivers from BOM

ejo4041, 2020-04-11:
I'm new to this project and building my first plotter.  I didn't realize I needed the stepper drivers, even though there are two obvious spots for them on the board.  I ordered the A4988 Stepper Motor Driver on ebay, there are some available from more reputable places like Polulu:
https://www.pololu.com/product/1182

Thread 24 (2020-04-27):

File types and software are suitable

admin-kepo, 2020-04-27:
I've been looking for various kinds of files that are suitable to be applied on this device, but the new I can only type G-Code only.
I really want this device to be able to write to change my hand to write it, but apparently I'm still constrained by how to make the g-code file itself.
before I had used inkscape and then converted it into unicord gcode, it didn't work. Is there someone who can help me find how I can create a gcode for this machine to write a paragraph?
please help !

Closed 2020-04-29.

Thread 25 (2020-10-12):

Servo setup instructions inconsistent

scruss, 2020-10-12:
In [Setting Up the Motors](https://github.com/bdring/midTbot_esp32/wiki/Setting-Up-the-Motors) - [Pen Servo Setup](https://github.com/bdring/midTbot_esp32/wiki/Setting-Up-the-Motors#pen-servo-setup) - [Test the Motion](https://github.com/bdring/midTbot_esp32/wiki/Setting-Up-the-Motors#test-the-motion), it says:

> …  Not all servos travel the same way. If yours is going the wrong way, send $3=4 to reverse the Z direction.

According to [$Stepper/StepInvert or $2 – Step port invert, mask](https://github.com/bdring/Grbl_Esp32/wiki/Settings#stepperstepinvert-or-2--step-port-invert-mask), that would invert Z but revert Y. With the default for the midTbot_esp32 being `$3=2`, wouldn't setting `$3=6` (invert *both* Y and Z) be required?

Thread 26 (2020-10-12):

No Pen Lift in Z0 .. Z5 range

scruss, 2020-10-12:
Following instructions in [Pen Servo Setup](https://github.com/bdring/midTbot_esp32/wiki/Setting-Up-the-Motors#pen-servo-setup), servos (both MG90 and SG90 tried)  do not respond to `G0Z0` or `G0Z5`. `G0Z-180` results in a slow, juddering movement in the servo from 0 to ~90° clockwise. `$HZ` results in a prompt return to home, while `G0Z0` is slow.

## Boot messages

    [MSG:Grbl_ESP32 Ver 1.3a Date 20201004]
    [MSG:Compiled with ESP32 SDK:v3.2.3-14-gd3e562907]
    [MSG:Using machine:MIDTBOT]
    [MSG:Axis count 3]
    [MSG:RMT Steps]
    [MSG:Init Motors]
    [MSG:X  Axis Standard Stepper Step:GPIO(12) Dir:GPIO(26) Disable:None Limits(0.000,100.000)]
    [MSG:Y  Axis Standard Stepper Step:GPIO(14) Dir:GPIO(25) Disable:None Limits(-100.000,0.000)]
    [MSG:Z  Axis RC Servo Pin:27 Pulse Len(3276,6553) Limits(-100.000,0.000)]
    [MSG:Global stepper disable pin:GPIO(13)]
    [MSG:No spindle]
    [MSG:Client Started]
    [MSG:Connecting CB283W]
    [MSG:Connecting.]
    [MSG:Connecting..]
    [MSG:Connected with 192.168.2.134]
    [MSG:Start mDNS with hostname:http://grblesp.local/]
    [MSG:SSDP Started]
    [MSG:HTTP Started]
    [MSG:TELNET Started 23]
    [MSG:X  Axis limit switch on pin GPIO(2)]
    [MSG:Y  Axis limit switch on pin GPIO(4)]
    [MSG:'$H'|'$X' to unlock]

## Grbl_Esp32 settings

    $Sta/SSID=CB283W
    $Sta/Password=******
    $Sta/IPMode=DHCP
    $Sta/IP=0.0.0.0
    $Sta/Gateway=0.0.0.0
    $Sta/Netmask=0.0.0.0
    $AP/SSID=GRBL_ESP
    $AP/Password=******
    $AP/IP=192.168.0.1
    $AP/Channel=1
    $System/Hostname=grblesp
    $Http/Enable=ON
    $Http/Port=80
    $Telnet/Enable=ON
    $Telnet/Port=23
    $Radio/Mode=STA
    $Bluetooth/Name=btgrblesp
    $Notification/Type=NONE
    $Notification/T1=
    $Notification/T2=
    $Notification/TS=
    $Homing/Cycle5=
    $Homing/Cycle4=
    $Homing/Cycle3=
    $Homing/Cycle2=
    $Homing/Cycle1=X
    $Homing/Cycle0=Y
    $Report/StallGuard=
    $Spindle/Type=NONE
    $Stepper/Pulse=3
    $Stepper/IdleTime=255
    $Stepper/StepInvert=
    $Stepper/DirInvert=Y
    $Stepper/EnableInvert=Off
    $Limits/Invert=On
    $Probe/Invert=Off
    $Report/Status=1
    $GCode/JunctionDeviation=0.010
    $GCode/ArcTolerance=0.002
    $Report/Inches=Off
    $Limits/Soft=Off
    $Limits/Hard=Off
    $Homing/Enable=On
    $Homing/DirInvert=X
    $Homing/Squared=
    $Homing/Feed=200.000
    $Homing/Seek=1000.000
    $Homing/Debounce=250.000
    $Homing/Pulloff=3.000
    $GCode/MaxS=1000.000
    $GCode/MinS=0.000
    $GCode/LaserMode=Off
    $GCode/Line1=
    $GCode/Line0=
    $Spindle/Enable/Invert=Off
    $Spindle/Enable/OffWithSpeed=Off
    $Spindle/Delay/SpinDown=0.000
    $Spindle/Delay/SpinUp=0.000
    $Spindle/PWM/Invert=Off
    $Spindle/PWM/Frequency=5000.000
    $Spindle/PWM/Off=0.000
    $Spindle/PWM/Min=0.000
    $Spindle/PWM/Max=100.000
    $X/StepsPerMm=200.000
    $Y/StepsPerMm=100.000
    $Z/StepsPerMm=100.000
    $A/StepsPerMm=100.000
    $B/StepsPerMm=100.000
    $C/StepsPerMm=100.000
    $X/MaxRate=8000.000
    $Y/MaxRate=8000.000
    $Z/MaxRate=5000.000
    $A/MaxRate=1000.000
    $B/MaxRate=1000.000
    $C/MaxRate=1000.000
    $X/Acceleration=200.000
    $Y/Acceleration=200.000
    $Z/Acceleration=100.000
    $A/Acceleration=200.000
    $B/Acceleration=200.000
    $C/Acceleration=200.000
    $X/Home/Mpos=0.000
    $Y/Home/Mpos=0.000
    $Z/Home/Mpos=0.000
    $A/Home/Mpos=0.000
    $B/Home/Mpos=0.000
    $C/Home/Mpos=0.000
    $X/MaxTravel=100.000
    $Y/MaxTravel=100.000
    $Z/MaxTravel=100.000
    $A/MaxTravel=300.000
    $B/MaxTravel=300.000
    $C/MaxTravel=300.000
    $X/Current/Run=0.250
    $Y/Current/Run=0.250
    $Z/Current/Run=0.250
    $A/Current/Run=0.250
    $B/Current/Run=0.250
    $C/Current/Run=0.250
    $X/Current/Hold=0.125
    $Y/Current/Hold=0.125
    $Z/Current/Hold=0.125
    $A/Current/Hold=0.125
    $B/Current/Hold=0.125
    $C/Current/Hold=0.125
    $X/Microsteps=16
    $Y/Microsteps=16
    $Z/Microsteps=16
    $A/Microsteps=16
    $B/Microsteps=16
    $C/Microsteps=16
    $X/StallGuard=16
    $Y/StallGuard=16
    $Z/StallGuard=16
    $A/StallGuard=16
    $B/StallGuard=16
    $C/StallGuard=16

bdring, 2020-10-12:
I think you just need to optimize the range, homing mpos homing direction.

https://github.com/bdring/Grbl_Esp32/wiki/Machine-Space-and-Homing
https://github.com/bdring/Grbl_Esp32/wiki/Servo-Axis-Feature

AndyRockall, 2021-03-17:
I'm having the same problem, has anyone solved this yet.
I'm using the same electronic/mechanical setup as in Bart's setup and build instructions.
I'm using Vers 2 of the board and the new pen lift, everything works except the pen lift servo.
I've checked, double checked and triple checked everything and am starting to tear my hair out (what's left of it).

Bart,
Have you tried your MidTbot with the new version of GRBL_ESP32?
If you have and it works could you perhaps publish your settings somewhere?

bdring, 2021-03-17:
I updated mine and used it within the last week. Have you read this page?

https://github.com/bdring/Grbl_Esp32/wiki/Servo-Axis-Feature

Is the Z not moving at all?

Paste your boot messages here. I can look at them.

https://github.com/bdring/Grbl_Esp32/wiki/Requesting-Help#boot-messages

AndyRockall, 2021-03-18:
No the Z isn't moving at at all.
boot messages below

[MSG:Grbl_ESP32 Ver 1.3a Date 20210226]
[MSG:Compiled with ESP32 SDK:v3.3.4-432-g7a85334d8]
[MSG:Using machine:midTbot]
[MSG:Axis count 3]
[MSG:RMT Steps]
[MSG:Init Motors]
[MSG:Global stepper disable pin:GPIO(13)]
[MSG:X  Axis Standard Stepper Step:GPIO(12) Dir:GPIO(26) Disable:None Limits(5.000,205.000)]
[MSG:Y  Axis Standard Stepper Step:GPIO(14) Dir:GPIO(25) Disable:None Limits(-150.000,0.000)]
[MSG:Z  Axis RC Servo Pin:27 Pulse Len(3276,6553) Limits(5.000,10.000)]
[MSG:Servo Update Task Started]
[MSG:CoreXY (midTbot) Kinematics Init]
[MSG:No spindle]

[MSG:Client Started]
[MSG:Connecting sueandandy]
[MSG:Connecting.]
[MSG:Connecting..]
[MSG:Connecting...]
[MSG:Connecting....]
[MSG:Connected with 192.168.0.170]
[MSG:Connected with 192.168.0.170]
[MSG:Start mDNS with hostname:http://MidTbot.local/]
[MSG:SSDP Started]
[MSG:HTTP Started]
[MSG:TELNET Started 23]
[MSG:X  Axis limit switch on pin GPIO(2)]
[MSG:Y  Axis limit switch on pin GPIO(4)]

bdring, 2021-03-18:
Send $Z and paste the response here.

AndyRockall, 2021-03-18:
$Z/RcServo/Cal/Max=1.000
$Z/RcServo/Cal/Min=1.000
$Z/StepsPerMm=100.000
$Z/MaxRate=5000.000
$Z/Acceleration=100.000
$Z/Home/Mpos=5.000
$Z/MaxTravel=5.000
$Z/Current/Run=0.250
$Z/Current/Hold=0.125
$Z/Microsteps=16
$Z/StallGuard=16
ok

bdring, 2021-03-18:
Is the servo locked or can you easily turn it by hand?

Also, send $Homing and paste the response.

AndyRockall, 2021-03-18:
The servo doesn't seem to be locked, I also measured the voltages and have 5V supply and about 0.04V on the signal pin.

$Homing/Cycle0=Z
$Homing/Cycle1=Y
$Homing/Cycle2=X
$Homing/Cycle3=
$Homing/Cycle4=
$Homing/Cycle5=
$Homing/Enable=On
$Homing/DirInvert=XZ
$Homing/Squared=
$Homing/Feed=500.000
$Homing/Seek=2000.000
$Homing/Debounce=250.000
$Homing/Pulloff=3.000

bdring, 2021-03-18:
Try sending $Homing/DirInvert=X

Then reset the ESP32 and show me the boot text.

I would like to see this
[MSG:Z Axis RC Servo Pin:27 Pulse Len(3276,6553) Limits(5.000,10.000)]
change to this
[MSG:Z Axis RC Servo Pin:27 Pulse Len(3276,6553) Limits(0.000,5.000)]

AndyRockall, 2021-03-18:
Looks like you got what you expected.

MSG:Grbl_ESP32 Ver 1.3a Date 20210226]
[MSG:Compiled with ESP32 SDK:v3.3.4-432-g7a85334d8]
[MSG:Using machine:midTbot]
[MSG:Axis count 3]
[MSG:RMT Steps]
[MSG:Init Motors]
[MSG:Global stepper disable pin:GPIO(13)]
[MSG:X  Axis Standard Stepper Step:GPIO(12) Dir:GPIO(26) Disable:None Limits(5.000,205.000)]
[MSG:Y  Axis Standard Stepper Step:GPIO(14) Dir:GPIO(25) Disable:None Limits(-150.000,0.000)]
[MSG:Z  Axis RC Servo Pin:27 Pulse Len(3276,6553) Limits(0.000,5.000)]
[MSG:Servo Update Task Started]
[MSG:CoreXY (midTbot) Kinematics Init]
[MSG:No spindle]

AndyRockall, 2021-03-18:
Bart,
Just remembered I had to increase the X/Y steps per mm to 200 to get it to travel the correct distance, does this shed any light?

bdring, 2021-03-18:
Here is an invitation to our discord server. It might be easier to help you there.

There is a midtbot channel.

https://discord.gg/kFJTzHFN4y

AndyRockall, 2021-03-18:
Bart,
I decided to re-compile with VSC rather than Arduino IDE.
Hey Presto it now works!
Compiled with Arduino IDE again and it didn't work.

So it seems as if we have to compile with VSC for it to be successful..

Thanks for all your help and the late night (it was 4:30 AM when I went to bed), much to my wife's displeasure.

odaki, 2021-06-07:
This change may improve the situation.
https://github.com/bdring/Grbl_Esp32/pull/914

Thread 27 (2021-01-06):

Limit switches

dunkfordyce, 2021-01-06:
Hi,

I have used the files here to print and make my first plotter and in fact first use of grbl and the first thing I have 3d printed that is in some way useful!

Due to the PCB not being available and because I'm just learning I have put together the electronics on a bread board. Amazingly I have managed to get it drawing. Thank you for the excellent project.

I am now trying to get the limit switches working. In the schematic files in this repo the switches look like they are normally open, but the internet suggests that limit switches for this sort of application are normally closed and made open when the limit is hit. So should they be normally open or closed?

Thanks

bdring, 2021-01-07:
You can use either type. They can be inverted in the software by sending $Limits/Invert=On or Off

https://github.com/bdring/Grbl_Esp32/wiki/Settings#limitsinvert-or-5---limit-pins-invert-boolean

dunkfordyce, 2021-01-07:
Ah thankyou, I tried that but I didnt have any pull down resistors so I'm
not sure if it was ever going to work. I ended up changing my switches to
be normally closed as this document recommends
https://github.com/gnea/grbl/wiki/Wiring-Limit-Switches.

If I reset all my settings with `$rst=$` (so using defaults from midtbot.h)
and then do a $H the y axis correctly goes towards the center of the bot
and will stop at the limit, but after that, when it does the X homing, it
goes in the wrong direction (towards the right/positive X).

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

dunkfordyce, 2021-01-07:
One thing I have never understood with the instructions in this repo is which way around and where 0,0 should be!

I ended up with the pen side closest to me, and then moved the pen to the bottom left as my 0, 0. So that positive y goes away from me and positive X goes to my right. Is that correct? because if its not then all my questions are back to front and sideways.

bdring, 2021-01-08:
It does not matter where the machine 0,0 is, but positive Y should move towards the center and positive X should move to the right.

You can then manually jog to where you want the 0,0 and set it.

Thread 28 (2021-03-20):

Shorter mounting screws required for specified stepper motors

graumannteague, 2021-03-20:
Hello, I recently built a midTbot and it's working great. However, I found that with the steppers from StepperOnLine specified in the BOM, the M3 x 8mm button head screws were a millimeter or so too long for the threaded holes in the motors' faceplate. This leaves play between the carriage block, PCB, and motors.

I replaced these with M3 x 6mm button head screws, and this fixed the issue. Maybe this could be updated in the mechanical BOM?

Thanks!

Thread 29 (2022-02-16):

Problems with hr4988 stepper drivers

J-Wrobel, 2022-02-16:
Hello, first of all thanks for this great project!. Secondly, sorry for bringing it up here as it is not an issue with the project but I figured that maybe someone had experience with this kind of issue.

I ordered a4988 step sticks from two sources and both of them turned out to be selling hr4988 instead of a4988 chips. A bummer but I have seen people use them and even in 3d printers so I gave it a shot. I put them on a breadboard to set the current limiting and discovered that as soon as I put 5V between GND and VDD they draw about 1,5A on that line. When supplied with 3V3 the current is about .9-1A. Quite odd that all 3 of them work this way (I skipped one that had plain short between GND-VDD-SLEEP pins). To me it seems not probable that all have same issue provided they are from two sources (they have different silk screen). Anyone encountered this and knows if this can be solved somehow and used at least for some time before I get proper ones?

Setup on breadboard: I tried connecting 5V and 3V3 to GND-VDD, tried with and without 12V on VMOT side with no current draw on that line. Tried bridging SLEEP and RESET. Everything leads to excessive current on logic lines. I tried diode tests on board pins and found short only one 1 out of 4 boards.

Closed 2022-02-18.

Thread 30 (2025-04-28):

Pulley alignment

nikthefix, 2025-04-28:
Looking at the step file V2 the idler pulleys are slightly misaligned. Is this deliberate?

Thanks

nik

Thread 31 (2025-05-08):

Midtbot wrong Y distance

dinhtuanel, 2025-05-08:
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

My midtbot, when moving with the axis, the distance is not correct, for example when I move x = 10mm it is correct, but when I move y = 10mm it only moves 1/2. I don't know what the cause of the error is, although I have edited the configuration file many times but still can't fix it. Please help me.

 I use A4988 driver, stepper motor 1.8, pulley 20 teeth

[MSG:INFO: FluidNC v3.9.7 https://github.com/bdring/FluidNC]
[MSG:INFO: Compiled with ESP32 SDK:v4.4.7-dirty]
[MSG:INFO: Local filesystem type is spiffs]
[MSG:INFO: Configuration file:config.yaml]
[MSG:INFO: Machine midtbot stepstick]
[MSG:INFO: Board midtbot]
[MSG:INFO: SPI SCK:gpio.18 MOSI:gpio.23 MISO:gpio.19]
[MSG:INFO: SD Card cs_pin:gpio.5 detect:NO_PIN freq:8000000]
[MSG:INFO: Stepping:RMT Pulse:4us Dsbl Delay:0us Dir Delay:2us Idle Delay:250ms]
[MSG:INFO: Axis count 3]
[MSG:INFO: Shared stepper disable gpio.13]
[MSG:INFO: Axis X (10.000,130.000)]
[MSG:INFO:   Motor0]
[MSG:INFO:     stepstick Step:gpio.12 Dir:gpio.26 Disable:NO_PIN]
[MSG:INFO:  Neg Limit gpio.2:low:pu]
[MSG:INFO:   Motor1]
[MSG:INFO: Axis Y (250.000,350.000)]
[MSG:INFO:   Motor0]
[MSG:INFO:     stepstick Step:gpio.14 Dir:gpio.25:low Disable:NO_PIN]
[MSG:INFO:  Neg Limit gpio.4:low:pu]
[MSG:INFO:   Motor1]
[MSG:INFO: Axis Z (-5.000,0.000)]
[MSG:INFO:   Motor0]
[MSG:INFO:     rc_servo Pin:gpio.27 Pulse Len(1000,2000 period:1048575)]
[MSG:INFO:     Update timer for rc_servo at 20 ms]
[MSG:INFO:   Motor1]
[MSG:INFO: Kinematic system: midtbot]
[MSG:INFO: Connecting to STA SSID:EC-GUEST]
[MSG:INFO: Connecting.]
[MSG:INFO: Connecting..]
[MSG:INFO: Connected - IP is 172.16.1.127]
[MSG:INFO: WiFi on]
[MSG:INFO: Start mDNS with hostname:http://fluidnc.local/]
[MSG:INFO: HTTP started on port 80]
[MSG:INFO: Telnet started on port 23]

Thank you.

Closed 2025-05-10.

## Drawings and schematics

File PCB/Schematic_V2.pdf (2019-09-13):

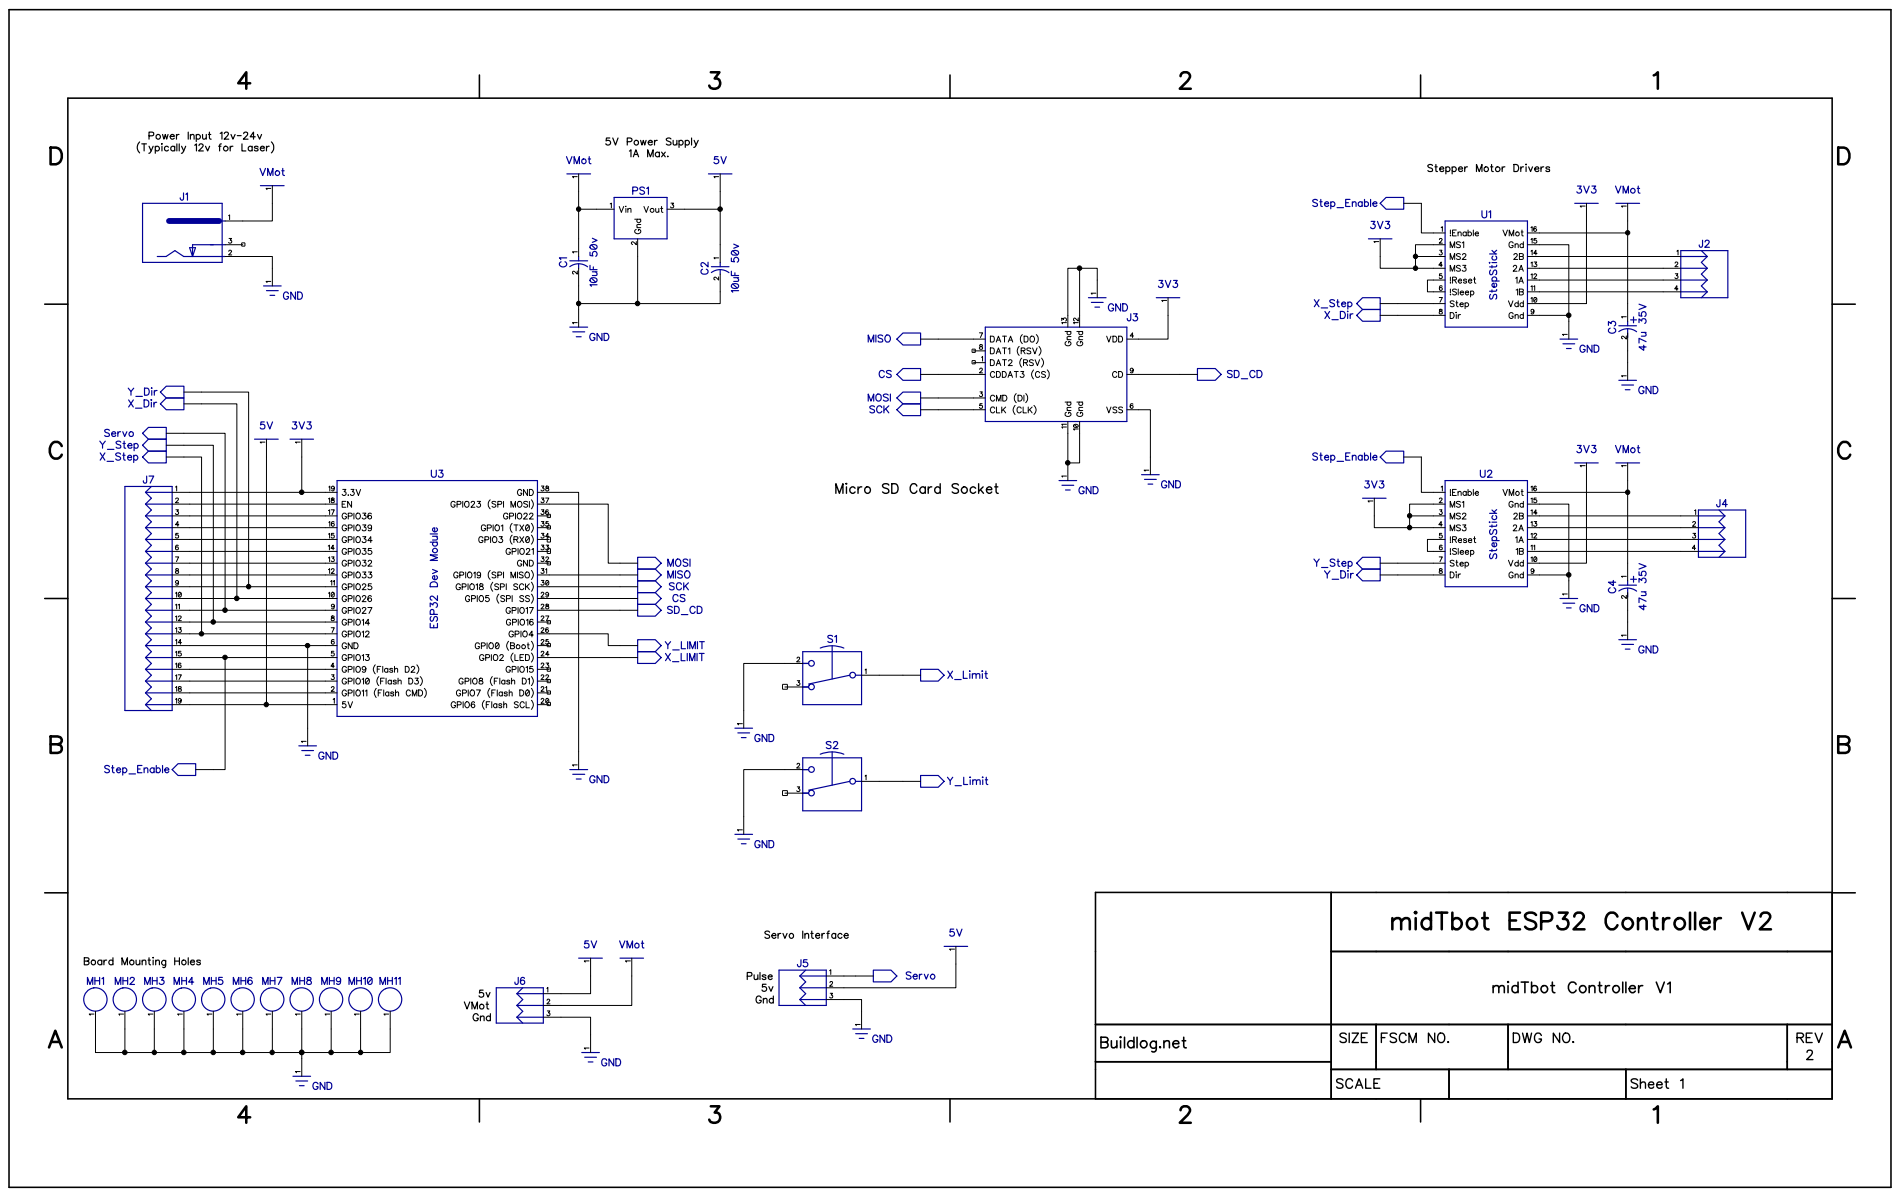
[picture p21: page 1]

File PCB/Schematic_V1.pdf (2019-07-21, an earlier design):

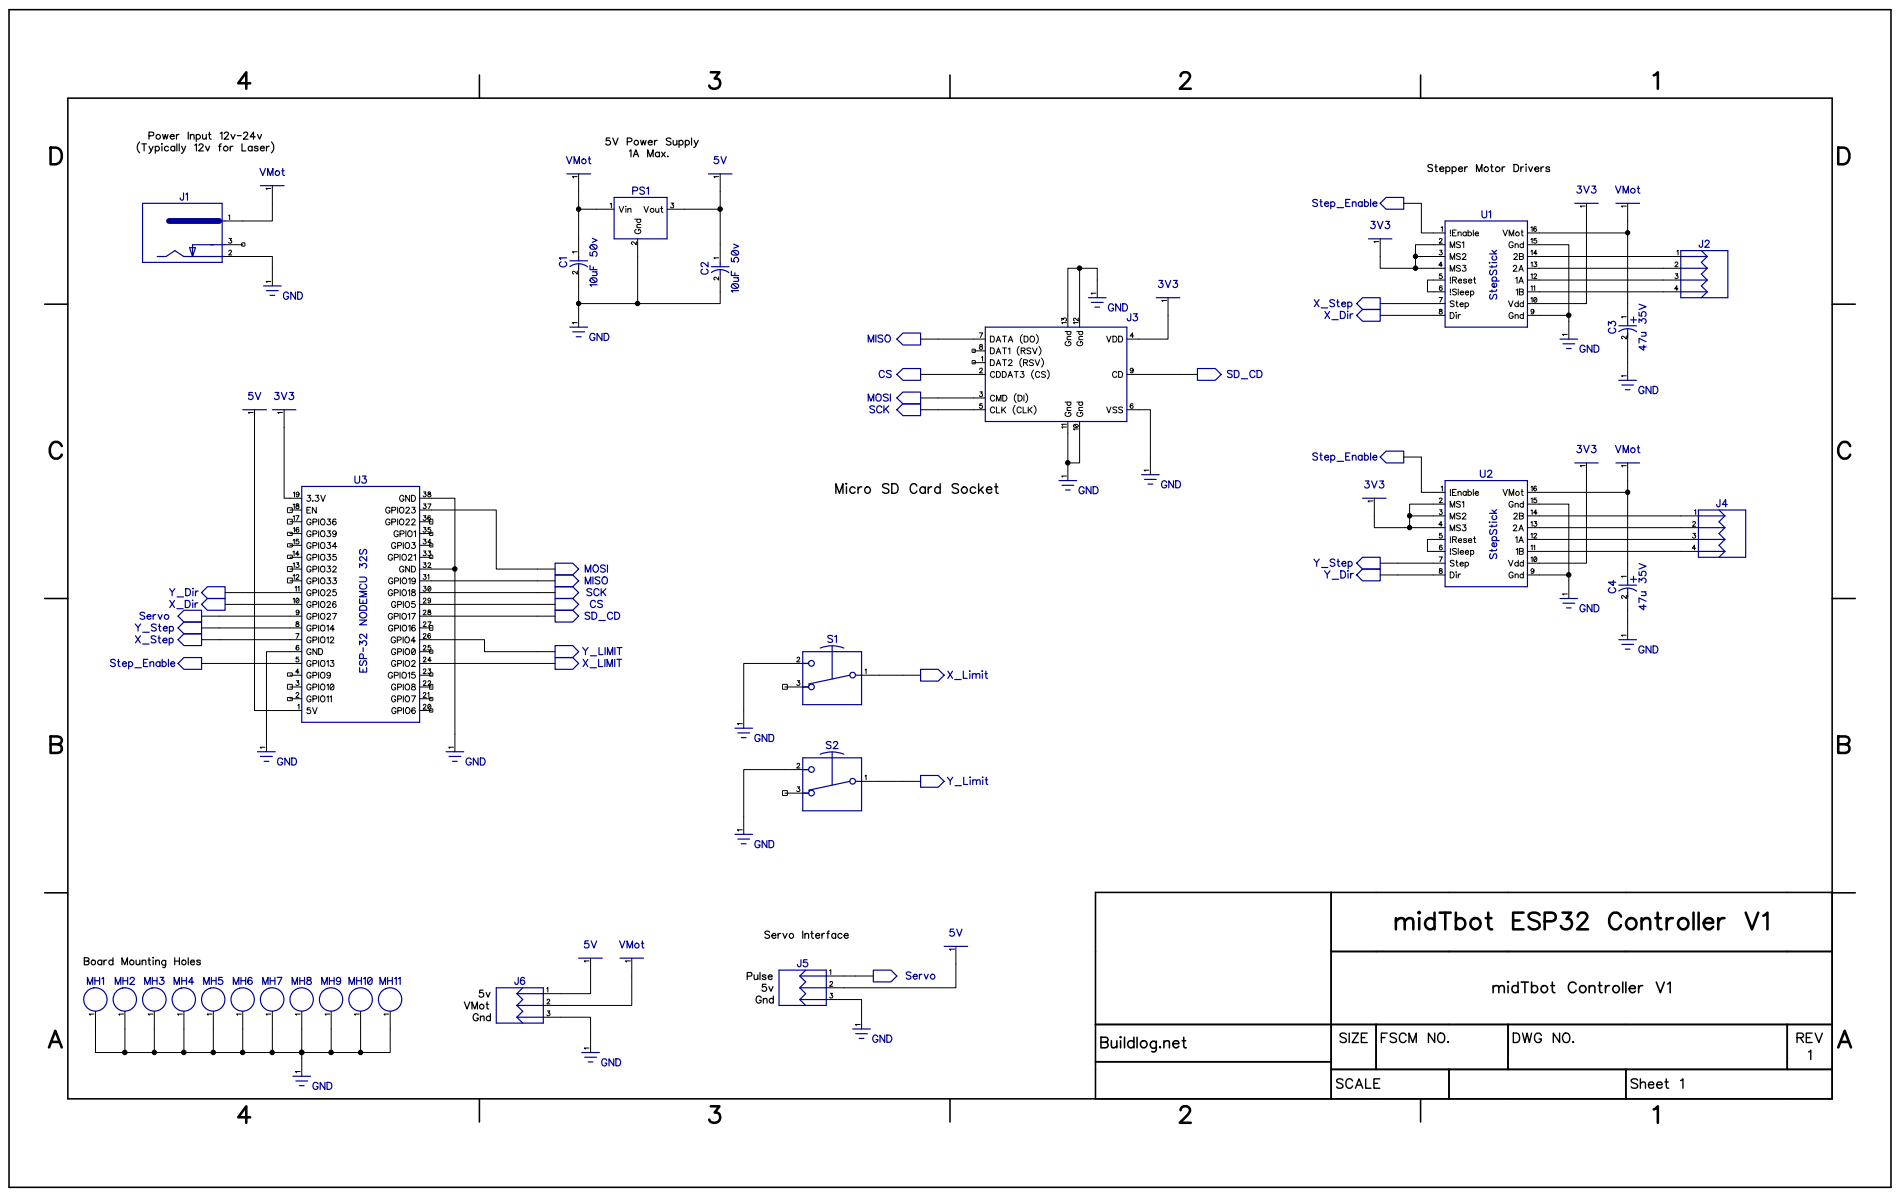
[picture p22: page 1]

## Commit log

2019-07-22 Added wiring image
2019-08-18 Modified to allow limit switches with mirrored levers to work
    - Standard switch sold out and is hard to get
    [midt_esp32_cover.stl, midt_esp32_left_foot.stl]
2019-08-18 Updated BOM with link to motor procurement discussion
2019-08-21 Adding files
    - Added solder stencil gerber
    - Added smaple gcode
    [TopPaste.gbr]
2019-09-13 Adding version 2 of the PCB
    [BoardOutline.gbr, Bottom.gbr, BottomMask.gbr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]
2020-03-16 Update StepperOnline link
    I think that website changed the URL for this product, please verify that it's the same thing, thanks!
